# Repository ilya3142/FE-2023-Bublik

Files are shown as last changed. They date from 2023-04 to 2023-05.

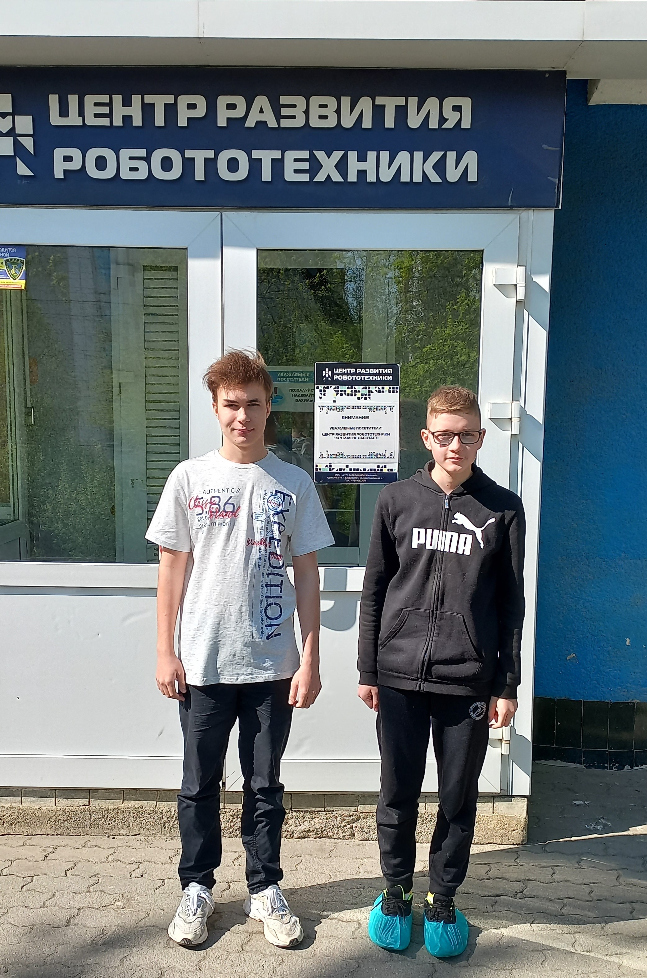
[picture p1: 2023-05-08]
Фото/Фото команды.jpg

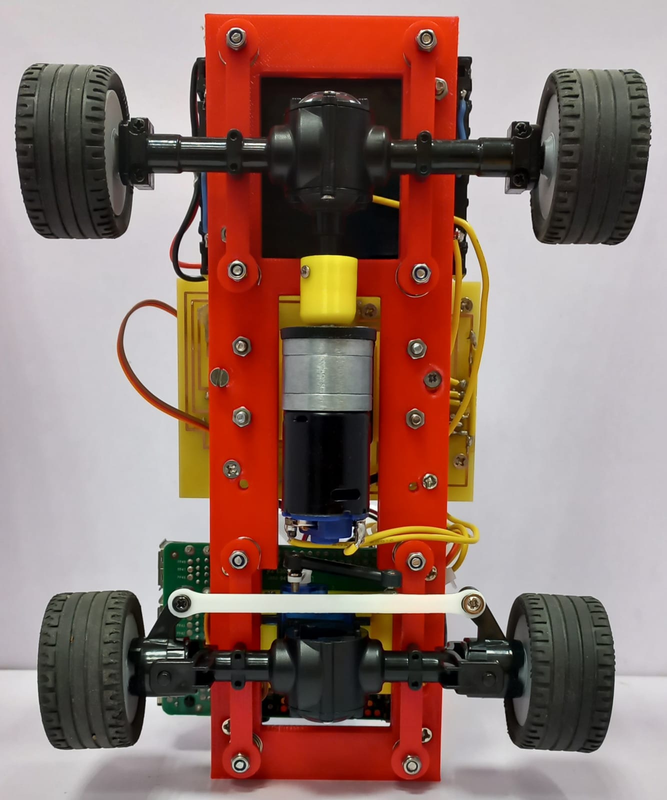
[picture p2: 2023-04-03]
Фото/вид снизу.jpg

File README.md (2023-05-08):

Расположение файлов, что находится в каждой папке

1. В папке 3D расположены модели деталей для нашего робота, которые мы сами моделировали и печатали на 3D принтере. Там есть следующие детали: диск (необходимо 4 шт. на одного робота), крепление под камеру (1 шт.), переходник с мотора (1 шт.) и рессора (4 шт.). 
2. В папке "src" расположены все фотографии, необходимые для пояснения того, как подключиться к нашему роботу и запустить программу. 
3. В папке "Видео" находится файл, загруженный на видеохостинг "YouTube", в котором показывается оба заезда (квалификационный и финальный) и краткое описание нашего робота. 
4. Папка "Код" содержит весь, необходимый для запуска, программный код, который включает в себя файлы: autostart.py (запуск программ квалификации и финала на соревнованиях), RobotAPI.py (считывание, вывод и редактирование изображения с камеры), Final.py (программа выступления в финальном заезде), kvalifikacia.py (программа выступления на квалификационном заезде), main.py (функции «нижнего кода») и start_robot.py (позволяет подключаться к роботу по сети Wi-Fi, загружать и запускать все программы). 
5. В папке "Технический журнал" находится вся документация, которая включает в себя:
	1. Реализация системы перемещения.
	2. Реализация системы питания и сенсоров.
	3. Реализация систем распознавания препятствий. 
 6. В папке "Фото" содержатся 6 фотографий робота с различных сторон и наша командная фотография.
 
Описание модулей кода

1. В программе «main.py» расположены функции «нижнего кода», а именно: 
	1. С Raspberry передает данные на драйвер мотора, светодиод.
	2. Передает показания с кнопки обратно на Raspberry.
2. Программа «start_robot.py» это приложение, позволяет подключаться к роботу по сети Wi-Fi, загружать и запускать все программы.
3. Файл «kvalificacia.py» содержит программу выступления на квалификационном заезде. 	Ниже представлено описания данного заезда: 
	Робот начинает движение по ПД регулятору считывая информацию о стенах с камеры. Когда он перестаёт видеть правую стену, он начинает поворачивать направо, а когда не видит левую, поворачивать налево. В процессе поворота робот должен увидеть на трассе первую одну из двух линий: либо синюю, либо оранжевую (с этого момента у робота включается счётчик линий того цвета, которую он увидел первым). Если он видит сначала синюю, то робот понимает, что движется против часовой стрелки, а если оранжевую, то по часовой. Во время движения вдоль каждой из 4 сторон, робот записывает время, за которое он проехал каждую прямую. Когда счётчик покажет, что робот увидел 12 раз синюю или оранжевую линию (в зависимости от направления движения), робот понимает, что проехал три круга, и ему нужно постепенно завершать заезд, он еще проезжает некоторое количество времени чтобы остановится идеально в зоне финиша, вычислив время проезда половины одной из двенадцати частей пути по записанному времени.
4. Файл «Final.py» содержит программу выступления в финальном заезде.
	Ниже представлено описание данного заезда:
	Робот начинает движение по ПД регулятору считывая информацию о стенах с камеры. Когда он перестаёт видеть правую стену, он начинает поворачивать направо, а когда не видит левую, поворачивать налево. В процессе поворота робот должен увидеть на трассе первую одну из двух линий: либо синюю, либо оранжевую (с этого момента у робота включается счётчик линий того цвета, которую он увидел первым). Если он видит сначала синюю, то робот понимает, что движется против часовой стрелки, а если оранжевую, то по часовой. Во время движения вдоль стен робот видит зелёные и красные знаки, если он видит зелёный знак, то объезжает его по левой стороне, а если красный – по правой. Когда счётчик покажет, что робот увидел 12 раз синюю или оранжевую линию (в зависимости от направления движения), робот понимает, что проехал три круга, и ему нужно постепенно завершать заезд, он еще проезжает некоторое количество времени чтобы остановится идеально в зоне финиша, вычислив время проезда половины одной из двенадцати частей пути по записанному времени.
5. Программа «autostart.py» необходима для запуска программ квалификации и финала на соревнованиях, сначала происходит автоматический запуск два раза квалификационного заезда, а затем два раза финального.
6. Файл «robotAPI.py» содержит функции, которые позволяют считывать и выводить картинку с камеры, делать определённые датчики на ней, которые необходимы для успешного проезда робота. 

Пошаговое объяснение, как подключиться к нашему роботу и запустить программу

1. Из папки "Код" на github скачиваем все файлы на компьютер. 
2. Загружаем файл "main.py" на Pyboard, для этого: подключаем Pyboard к компьютеру при помощи кабеля, находим на компьютере папку Pyboard и копируем туда файл "main.py". 
3. Открываем файл "start_robot.py" в PyCharm.
4. Далее запускаем этот файл.
5. Затем подключаемся к Raspberry нашего робота через сеть Wi-Fi. (https://github.com/ilya3142/FE-2023-Bublik/blob/main/src/image%201.png)
6. Затем у нас открывается окно "RoboStarter", где мы нажимаем кнопку "Connect to robot" и выбираем там нашего робота по названию.(https://github.com/ilya3142/FE-2023-Bublik/blob/main/src/image%202.png)
7. Далее мы нажимаем кнопку «Load Start», где мы можем выбрать и запустить программу, которая нам необходима: проезд финала, квалификации, или файл «autostart.py», в котором содержится одна из вышеперечисленных программ.

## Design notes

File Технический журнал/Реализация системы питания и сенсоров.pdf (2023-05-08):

### Реализация системы питания и сенсоров

### 1. Питание

| Напряжение | Ёмкость
Аккумулятор 18650 | 3.7 B | 3500 mAh
Аккумулятор 14500 | 3.7 В | 600 mAh
Батарейки AA | 1.2 В | 2100 mAh

Для питания нам было представлено три типа: аккумулятор 18650, аккумулятор 14500 и батарейки типа AA. Из них мы остановились на варианте аккумулятора 18650, так как у него наибольшая ёмкость и токоотдача, благодаря чему он дольше поддерживает работу. Выбрав аккумулятор, мы взяли три штуки и поместили их в отсек для того, чтобы получилось общее напряжение около 12 Вольт.

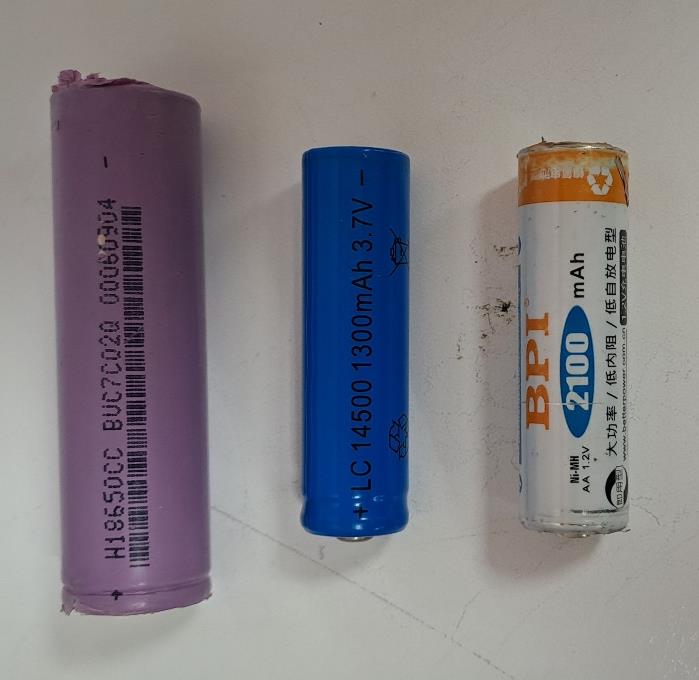
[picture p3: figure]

Слева направо:
1. Аккумулятор 18650
2. Аккумулятор 14500
3. Батарейка типа АА

### 2. Камера и Raspberry

Для того, чтобы распозновать все объекты на соревновании нам необходима камера. У нас было представлено три камеры на выбор:

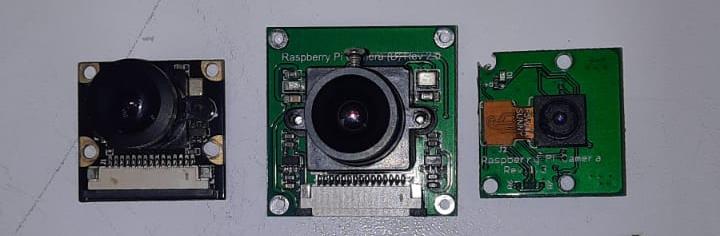
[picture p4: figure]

Слева направо:

1. RPi Camera G
2. RPi Camera B
3. RPi Camera Board

Исходя из их характеристик, мы пришли к решению выбрать камеру под номером 1, потому что она обладает наибольшим углом обзора, то есть является широкоугольной, что позволяет нам хорошо видеть бортики на игровом поле.

Для обработки и считывания изображения с камеры мы используем одноплатный компьютер Raspberry Pi 3B. Для распознавания объектов на соревновательном поле, мы используем язык программирования Python и библиотеку OpenCV. Благодаря им, мы можем на камере выделить области под датчики и распознавать объекты в разных частях изображения.

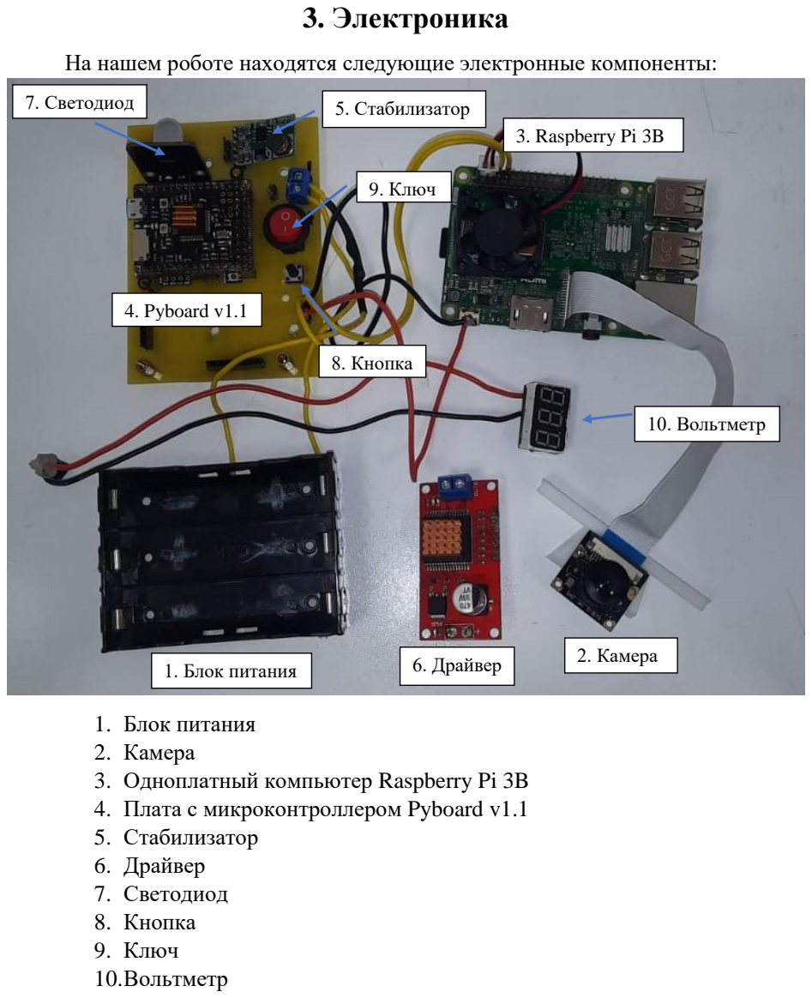
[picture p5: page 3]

### 3. Электроника

На нашем роботе находятся следующие электронные компоненты:

1. Блок питания
2. Камера
3. Одноплатный компьютер Raspberry Pi 3B
4. Плата с микроконтроллером Pyboard v1.1
5. Стабилизатор
6. Драйвер
7. Светодиод
8. Кнопка
9. Ключ
10.Вольтметр
10. Вольтметр
1. Блок питания | 6. Драйвер | 2. Камера
3. Raspberry Pi 3B
4. Pyboard v1.1
5. Стабилизатор 7. Светодиод
8. Кнопка
9. Ключ

### 4. Электрическая схема

Ниже представлена электрическая схема, сделанная на платформе EasyEDA, по ней вы можете разобраться, какие компоненты куда необходимо подключать:

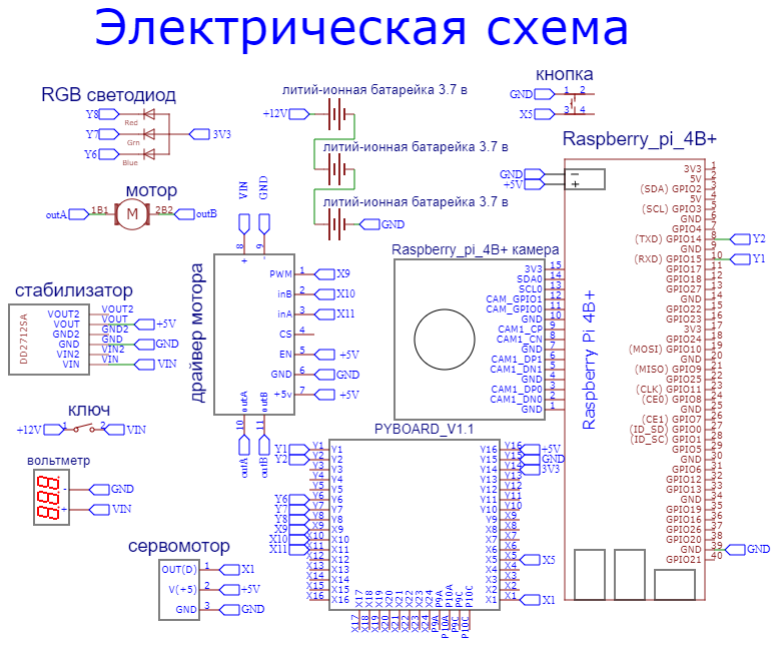
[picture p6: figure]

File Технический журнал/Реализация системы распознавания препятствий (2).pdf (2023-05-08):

Реализация системы распознавания препятствий

### 1. Квалификационный заезд

Ниже представлено описание проезда робота на квалификационном заезде:

Робот начинает движение по ПД регулятору считывая информацию о стенах с камеры. Когда он перестаёт видеть правую стену, он начинает поворачивать направо, а когда не видит левую, поворачивать налево. В процессе поворота робот должен увидеть на трассе первую одну из двух линий: либо синюю, либо оранжевую (с этого момента у робота включается счётчик линий того цвета, которую он увидел первым). Если он видит сначала синюю, то робот понимает, что движется против часовой стрелки, а если оранжевую, то по часовой. Во время движения вдоль каждой из 4 сторон, робот записывает время, за которое он проехал каждую прямую. Когда счётчик покажет, что робот увидел 12 раз синюю или оранжевую линию (в зависимости от направления движения), робот понимает, что проехал три круга, и ему нужно постепенно завершать заезд, он еще проезжает некоторое количество времени чтобы остановится идеально в зоне финиша, вычислив время проезда половины одной из двенадцати частей пути по записанному времени.

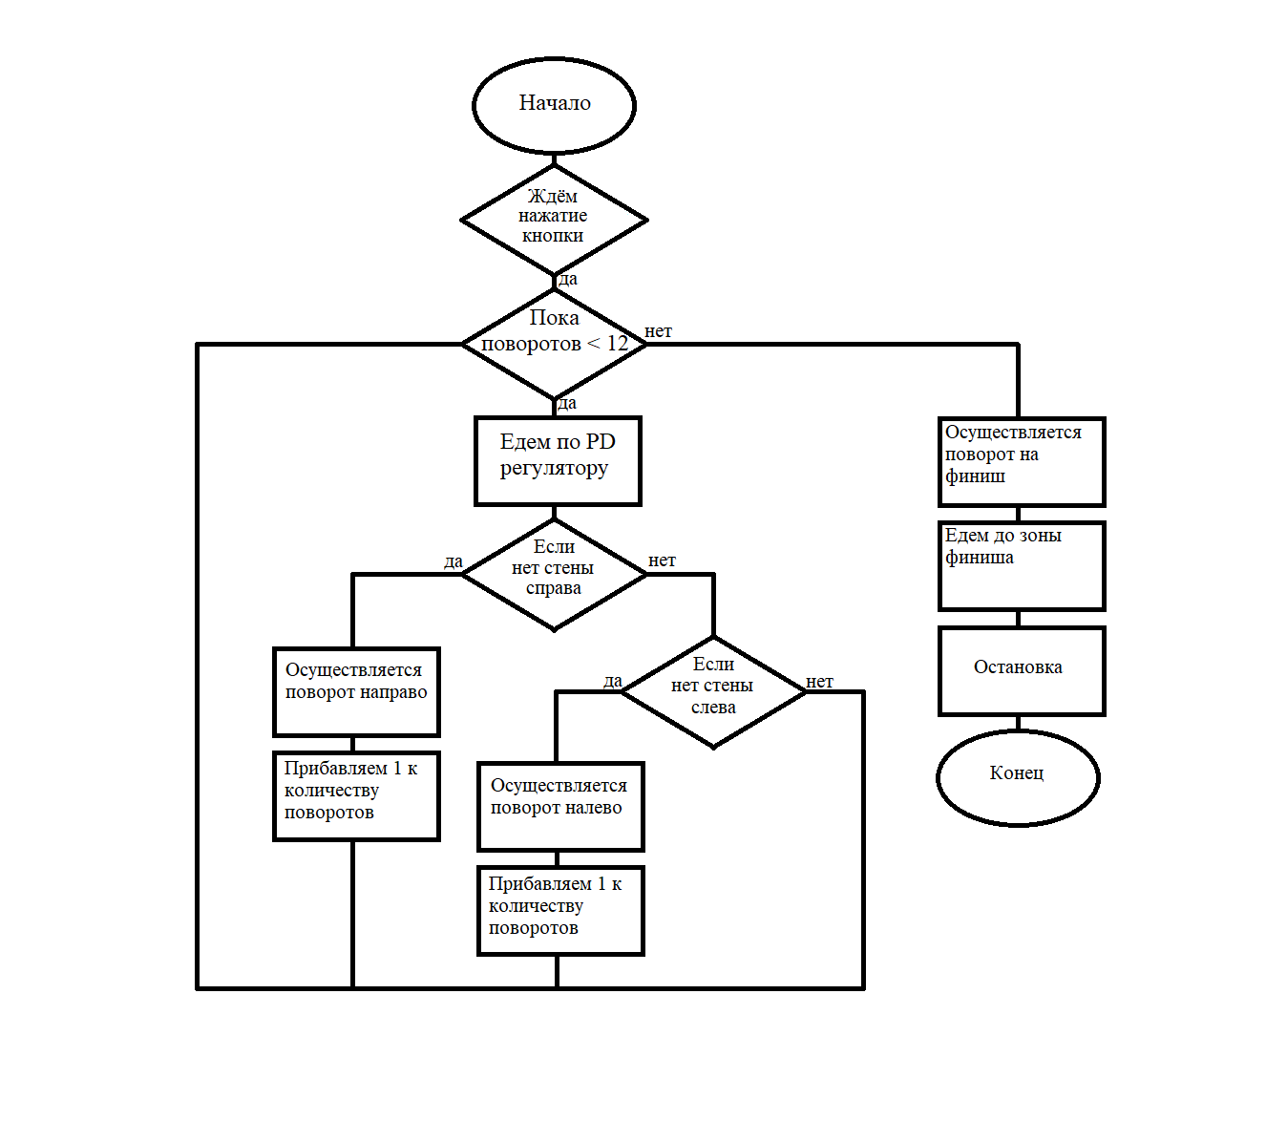
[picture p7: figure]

### 2. Финальный заезд

Ниже представлено описание проезда робота на финальном заезде:

Робот начинает движение по ПД регулятору считывая информацию о стенах с камеры. Когда он перестаёт видеть правую стену, он начинает поворачивать направо, а когда не видит левую, поворачивать налево. В процессе поворота робот должен увидеть на трассе первую одну из двух линий: либо синюю, либо оранжевую (с этого момента у робота включается счётчик линий того цвета, которую он увидел первым). Если он видит сначала синюю, то робот понимает, что движется против часовой стрелки, а если оранжевую, то по часовой. Во время движения по трассе робот видит зелёные и красные знаки, если он видит зелёный знак, то объезжает его по левой стороне, а если красный – по правой. Когда счётчик покажет, что робот увидел 12 раз синюю или оранжевую линию (в зависимости от направления движения), робот понимает, что проехал три круга, и ему нужно постепенно завершать заезд, он еще проезжает некоторое количество времени чтобы остановится идеально в зоне финиша, вычислив время проезда половины одной из двенадцати частей пути по записанному времени.

### 3. Распознавание знаков

На камере робот ищет красные и зелёные знаки в области интереса, которая находится в центре. При нахождении любого знака робот обводит больший знак соответствующим цветом (красный знак – жёлтая рамка, зелёный знак – розовая рамка).

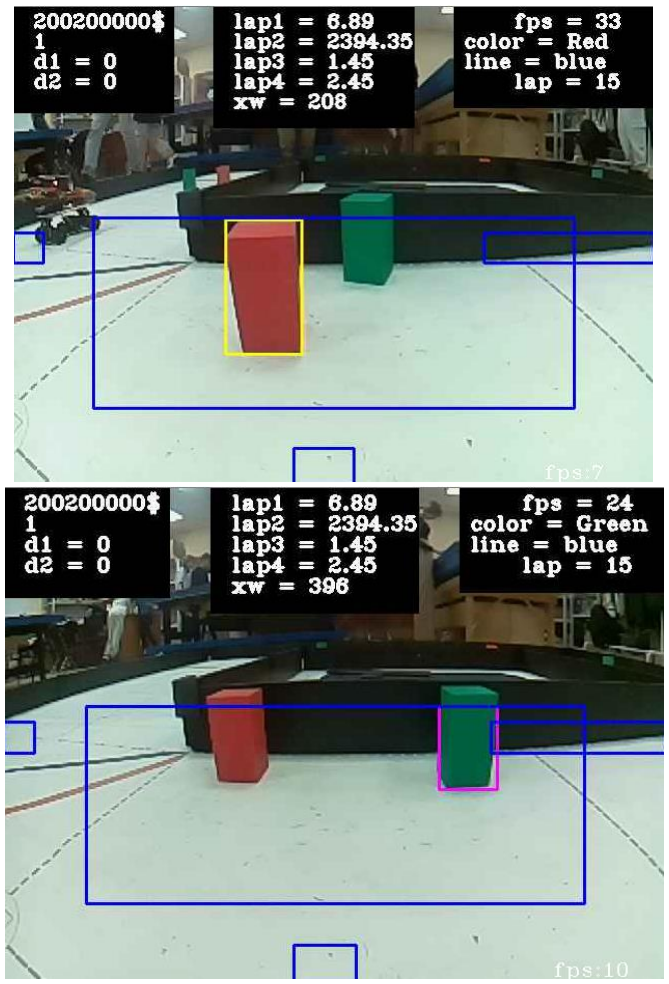
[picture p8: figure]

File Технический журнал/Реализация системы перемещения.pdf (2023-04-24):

### Реализация системы перемещения

### 1. Выбор моторов для движения

Изначально у нас было представлено на выбор 3 мотора:

1. GM25-370 на 6 вольт и 210 оборотов в минуту.

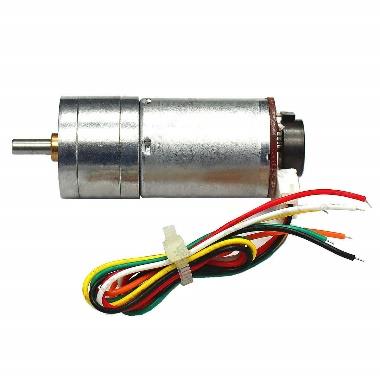
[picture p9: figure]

2. CH-N20-3 – 6 вольт и 500 оборотов в минуту.

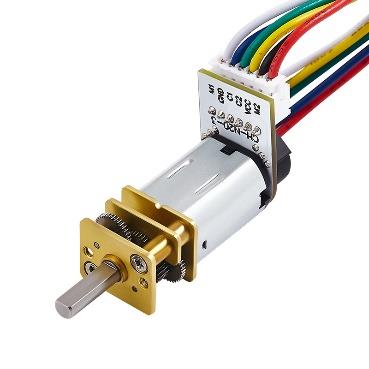
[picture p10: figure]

3. CHR-GM25-370 на 12 вольт и 980 оборотов в минуту.

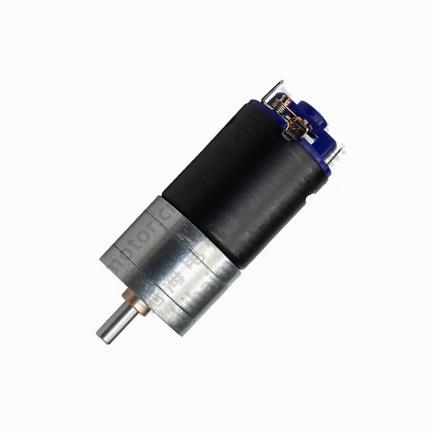
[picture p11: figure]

Мы выбрали третий вариант - CHR-GM25-370, потому что он обладает самыми хорошими и выгодными для нас характеристиками, а именно: металлической цилиндрической шестернёй, сильный магнитный крутящий момент и достаточно большой скоростью (980 об/мин). Также у него есть отдельное крепление, под которое удобно проектировать кузов.

### 2. Выбор моторов для руления

Нам также было представлено на выбор 3 мотора для руления:

1. Tower Pro SG90: Сервопривод с диапазоном 0-180° обладает компактными размерами, напряжение 3,5-6 вольт, весом 9 грамм и обладает большим крутящим моментом (до 1,6 кг·см). Механизм сервопривода выполнен из пластика.

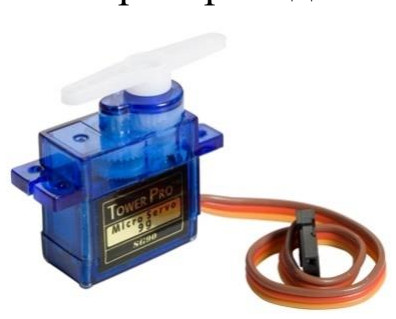
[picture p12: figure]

2. TIANKONGRC MG90D: управляется по сигналу PDM, способен удерживать угол от 0 до 180° и обладает крутящим моментом до 2,1 кг·см.

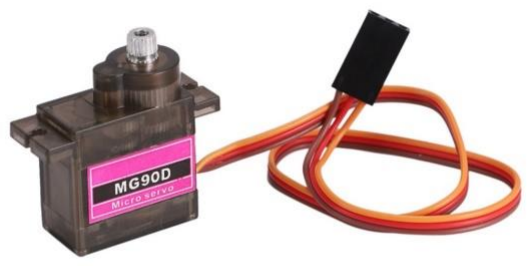
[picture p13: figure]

3. EMAX ES08A: рабочее напряжение 4,8-6 вольт, крутящий момент до 1,8 кг·см, Длина сервопривода от выхода корпуса до вилки: 230 мм, механизм выполнен из пластика

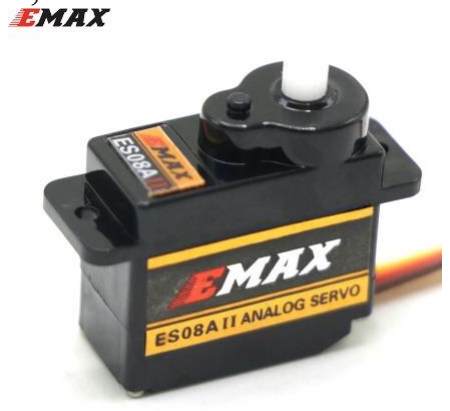
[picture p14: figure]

Все представленные модели обладают схожими характеристиками, поэтому мы выбрали первый вариант - Tower Pro SG90 из-за того, что это самый распространённый мотор, который, при необходимости, всегда можно заменить.

### 3. Подвеска

Мы выбирали между двумя видами подвески:

1. Мостовая: это такая подвеска, в которой ось связывает между собой два колеса. Колеса связаны через дифференциал.

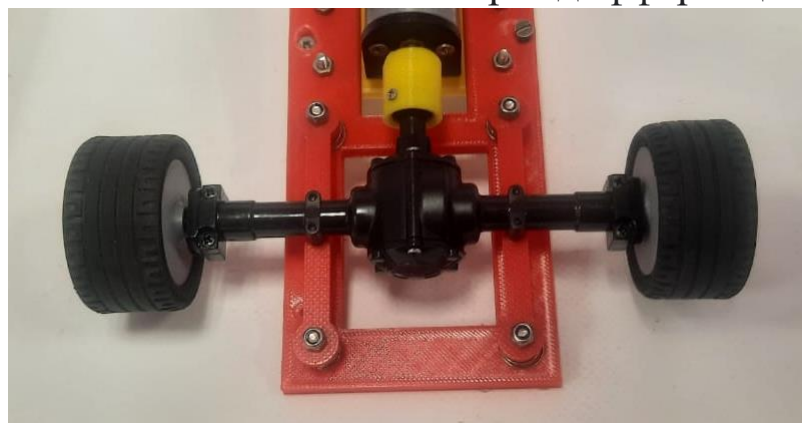
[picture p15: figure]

2. Независимая: это такая подвеска, в которой колеса одной оси не связаны друг с другом, и изменение положения одного колеса не оказывает влияния на другое.

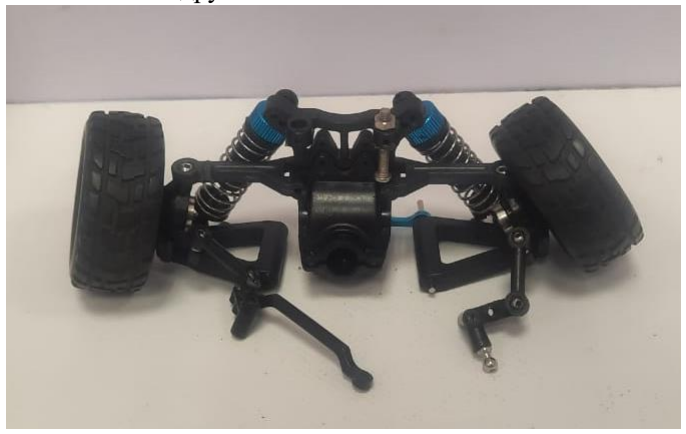
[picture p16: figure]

Для мостовой подвески было гораздо проще создать кузов, она была удобнее в креплении к основной раме робота, поэтому мы её и выбрали.

### 4. Колёса

При переходе к этому этапу мы столкнулись с проблемой, что колёса, которые шли в комплекте с подвеской оказались слишком большие для нашей машинки (56x25):

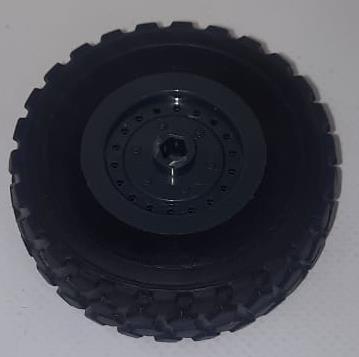
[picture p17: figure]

И поэтому мы спроектировали и распечатали на 3D принтере новые диски (31x20) оптимального размера и вставили их в шины (42x21):

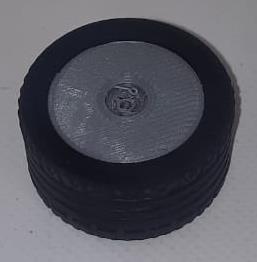
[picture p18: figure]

### 5. Рама робота

Для соединения всех механизмов и деталей, таких как рессоры, муфта и подвеска, в одно целое, мы спроектировали и распечатали на 3D принтере раму, которая связывает все элементы робота.

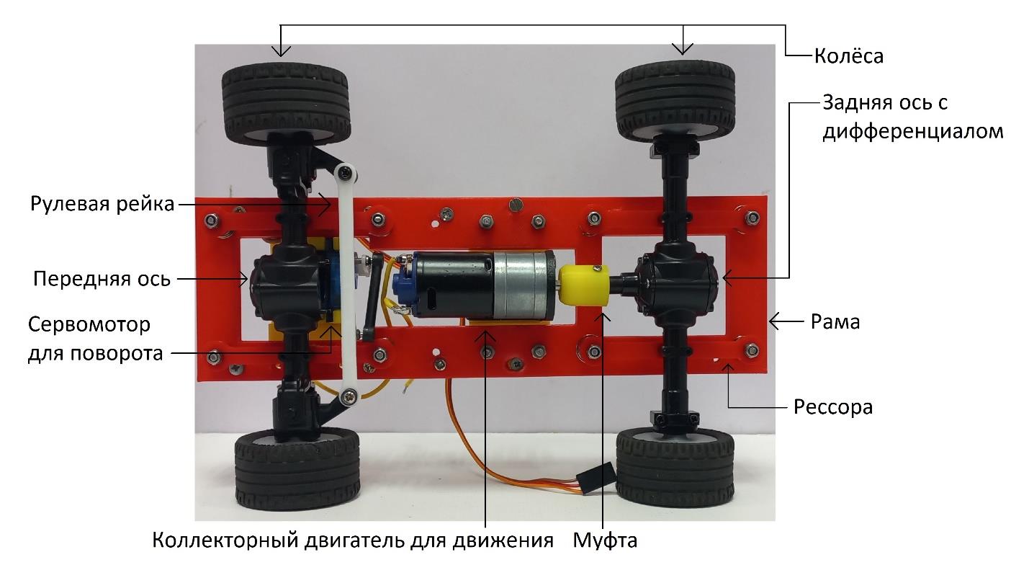
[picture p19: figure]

### 6. Механическая схема автомобиля

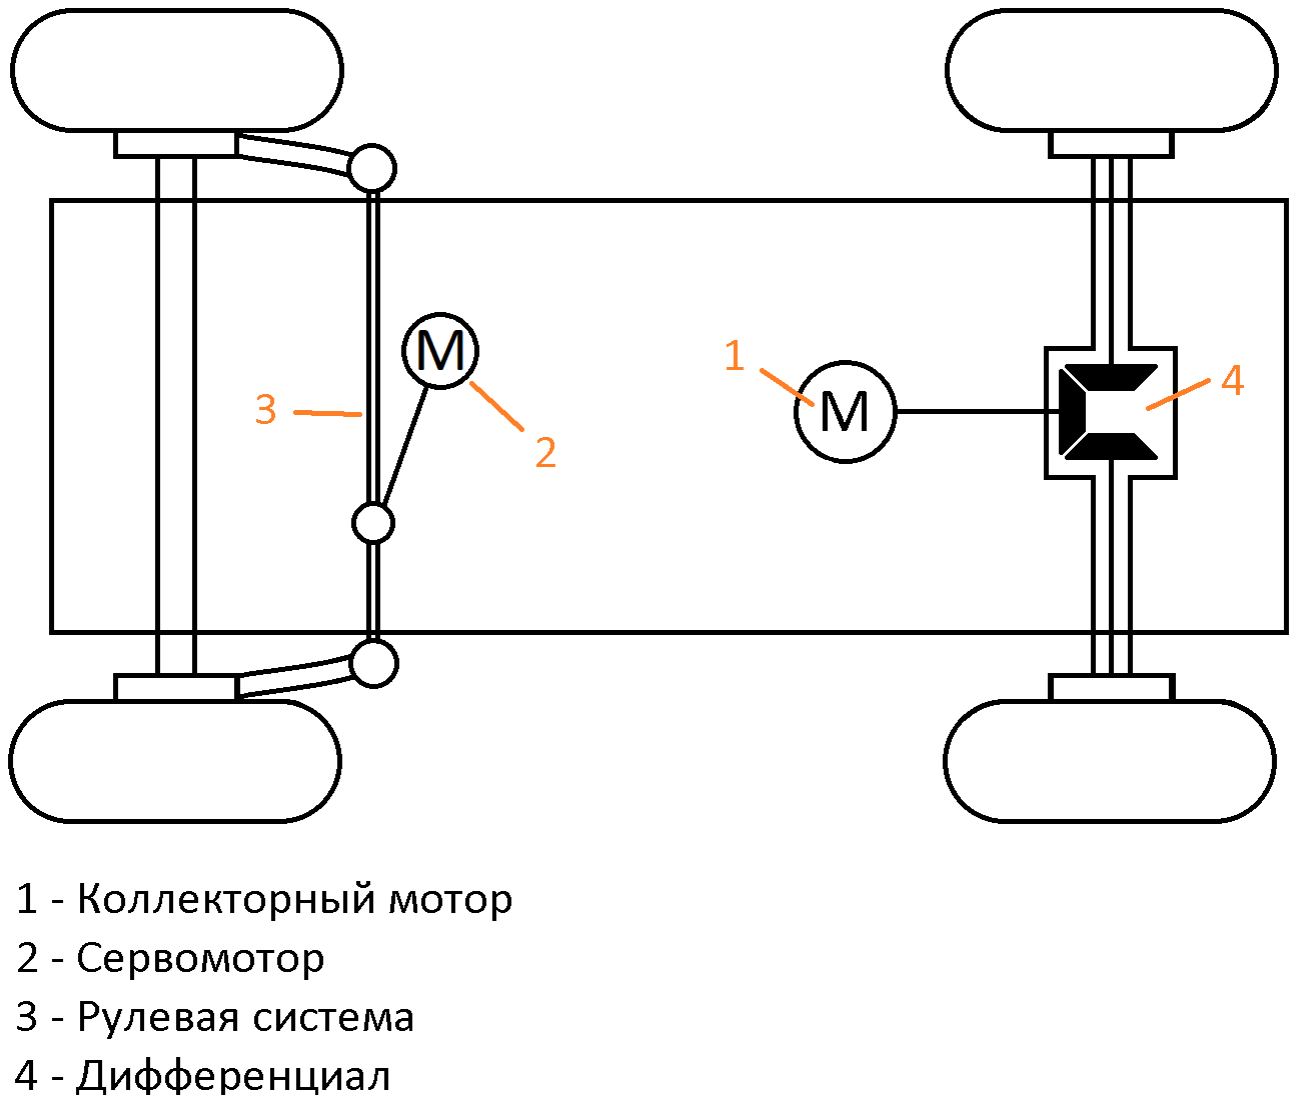
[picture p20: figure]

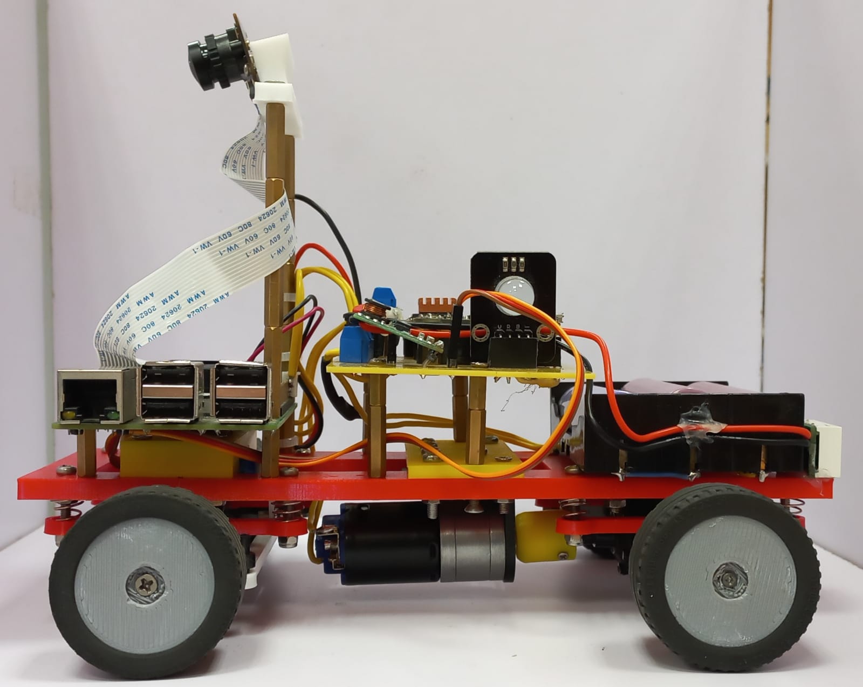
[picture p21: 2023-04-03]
Фото/вид слева.jpg

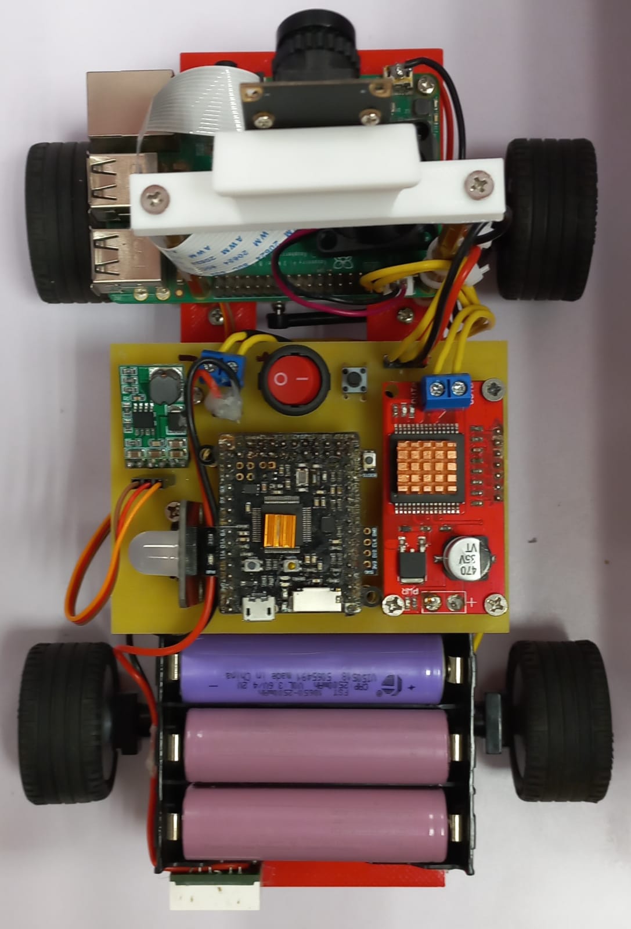
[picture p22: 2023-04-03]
Фото/вид сверху.jpg

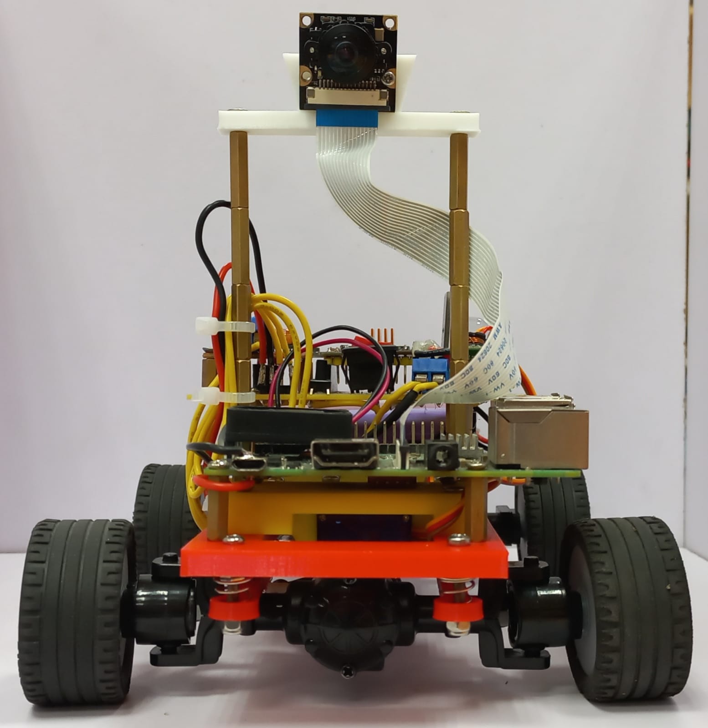
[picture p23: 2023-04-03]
Фото/вид спереди.jpg

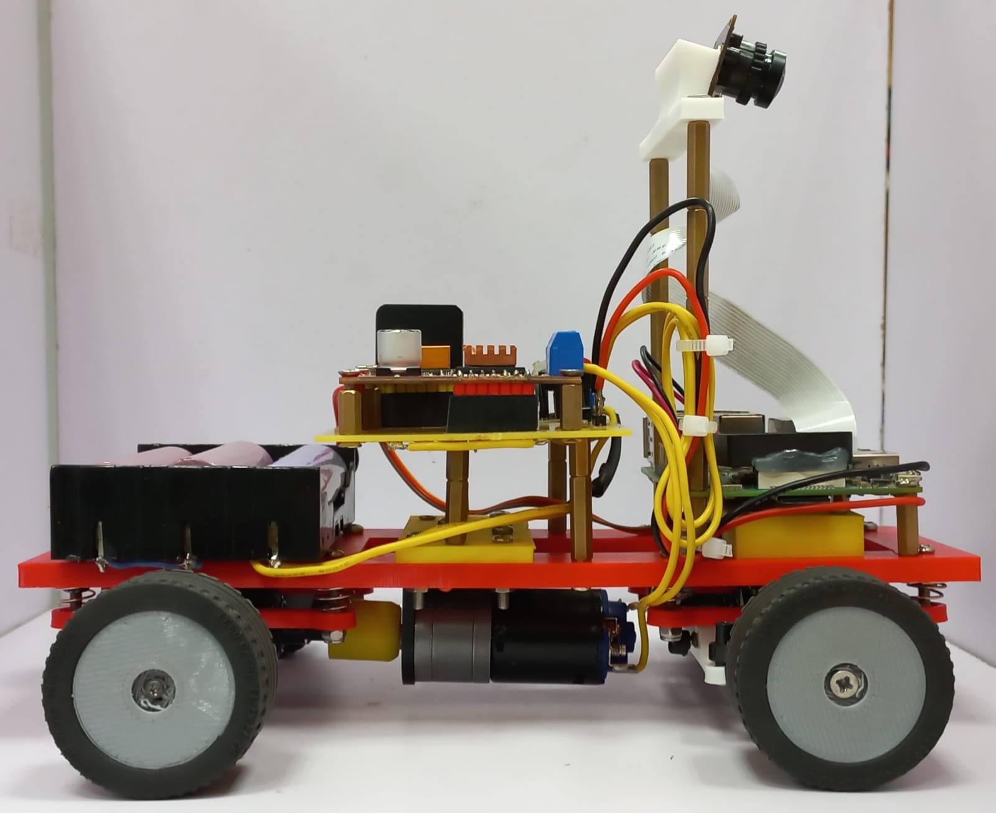
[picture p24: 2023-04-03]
Фото/вид справа.jpg

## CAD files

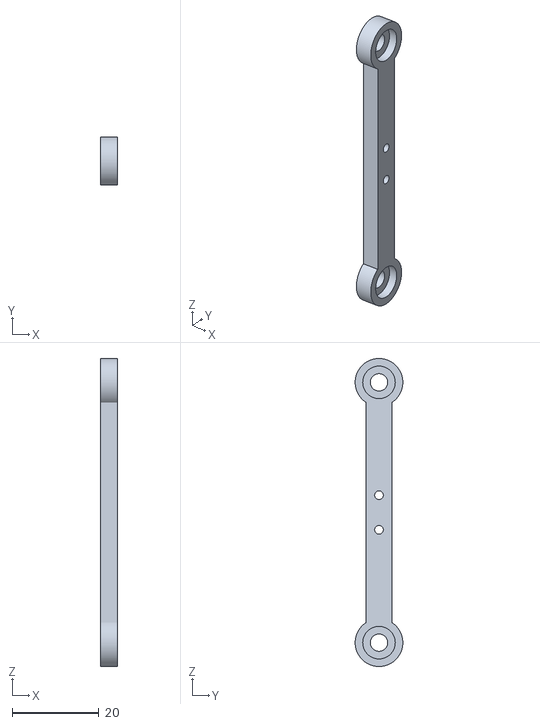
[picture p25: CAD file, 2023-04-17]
3D/рессора.stl
4.00 x 11.0 x 71.0

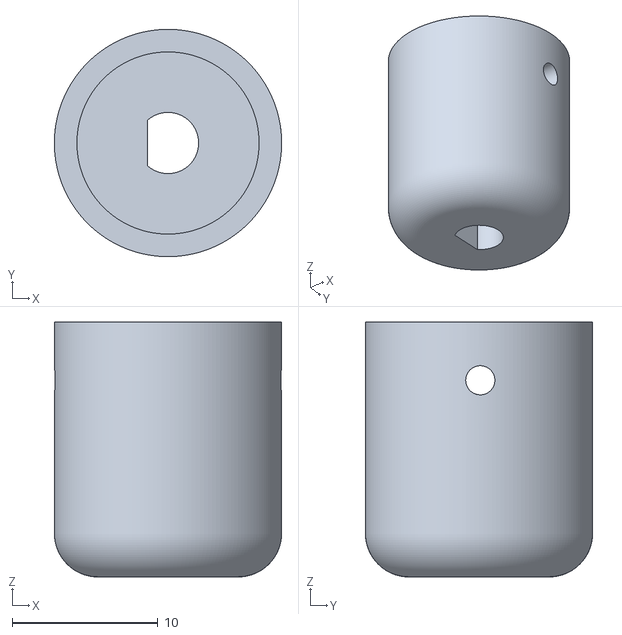
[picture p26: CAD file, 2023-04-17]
3D/переходник с мотора.stl
15.6 x 15.6 x 17.5

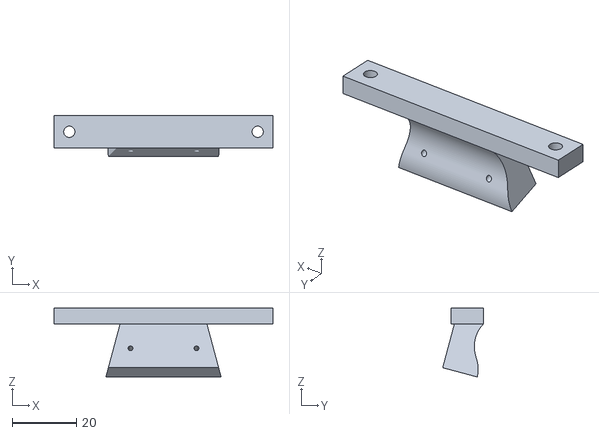
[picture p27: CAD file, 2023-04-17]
3D/крепление под камеру.stl
68.0 x 12.6 x 21.4

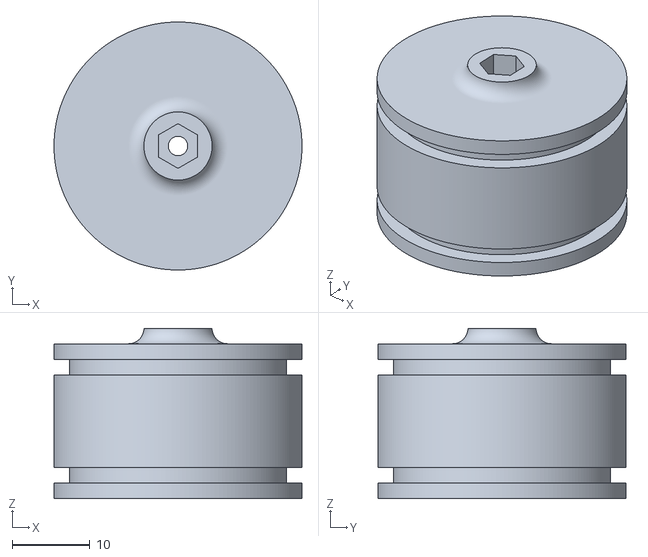
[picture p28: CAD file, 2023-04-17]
3D/диск.stl
32.0 x 32.0 x 22.0

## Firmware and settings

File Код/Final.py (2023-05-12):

import cv2
import RobotAPI as rapi
import numpy as np
import serial
import time
from array import *

tim_s = time.time()
tim_l = time.time()
tp = time.time()
ts = time.time()
tz = time.time()
tr = time.time()
tg = time.time()

fst = False

low_black=np.array([0,0,0]) # HSV чёрного
up_black=np.array([70,255,27])

low_red=np.array([0,130,0]) # HSV красного
up_red=np.array([5,220,255])

low_blue=np.array([93,108,56]) # HSV синего
up_blue=np.array([128,255,139])

low_orange=np.array([0,110,100]) # HSV оранжеаого
up_orange=np.array([20,255,182])

low_green=np.array([74, 168, 67]) # HSV зелёного
up_green=np.array([99, 255, 145])

port = serial.Serial("/dev/ttyS0", baudrate=115200, stopbits=serial.STOPBITS_ONE)
robot = rapi.RobotAPI(flag_serial=False)
robot.set_camera(100, 640, 480)

direction = "None" # направление движения

vrm= [0, 0, 0, 0]
vi = 0
message = ""
fps = 0
fps1 = 0
fps_time = 0

art = 0

x_zn = 0
y_zn = 0
w_zn = 0
h_zn = 0

r_zn = 0
g_zn = 0

zn_old = 0
zn_t = 0
wzn_old = 0


e_old = 0
e_old_zn = 0

kp = 0.15
kd = 0.15

d1 = 0
d2 = 0
d1old = 0
d2old = 0
d1t = 0
d2t = 0

color = 'Green'
line1 = 'Orange'
lap = 0

speed = 0 # скорость
serv = 0 # угол поворота сервомотора
rgb = "111" # сообщение для светодиода
inn = ""


xleft = 160
xright = 470

def znak(frame): # распознавание знаков
    global x_zn, y_zn, h_zn, w_zn,color, tz, xleft, xright, zn_t, zn_old, wzn_old
    x_zn, y_zn, h_zn, w_zn = 0, 0, 0, 0
    x1 = 80 # область интереса
    x2 = 560
    y1 = 210
    y2 = 400
    dat = frame[y1:y2, x1:x2]
    hsv = cv2.cvtColor(dat, cv2.COLOR_BGR2HSV) # преобразование BGR в HSV


    mask = cv2.inRange(hsv, low_red, up_red) # создание маски
    imd, contours, hod = cv2.findContours(mask, cv2.RETR_TREE, cv2.CHAIN_APPROX_NONE) # находим на маске контуры
    xx, yy, ww, hh = 0,0,0,0
    for contor in contours:
        x, y, w, h = cv2.boundingRect(contor) # обводим контуры
        if h*w > 100 and h*w > hh*ww:
            xx, yy, ww, hh = x,y,w,h




    mask1 = cv2.inRange(hsv, low_green, up_green) # создание маски
    imd, contours, hod = cv2.findContours(mask1, cv2.RETR_TREE, cv2.CHAIN_APPROX_NONE) # находим контуры на маске
    xq, yq, wq, hq = 0, 0, 0, 0
    for contor in contours:
        x, y, w, h = cv2.boundingRect(contor) # обводим контуры
        if h*w > 100 and h*w > hq*wq:
            xq, yq, wq, hq = x,y,w,h


    color = 'None'

    if hh > 0 or hq > 0: # изменение областей интересов для распознавания стен

        if yy + hh > yq + hq: # объезд знаков
            cv2.rectangle(dat, (xx, yy), (xx + ww, yy + hh), (0, 255, 255), 2) # обводим найденные когтуры
            x_zn, y_zn, w_zn, h_zn = xx, yy, ww, hh
            color = 'Red'
            if direction == "blue": # направление движения
                xleft = 30

        else:
            cv2.rectangle(dat, (xq, yq), (xq + wq, yq + hq), (255, 0, 255), 2) # обводим найденные контуры
            x_zn, y_zn, w_zn, h_zn = xq, yq, wq, hq
            color = 'Green'
            if direction == "orange": # направление движения
                xright = 610

        tz = time.time()
        zn_old = x_zn
        wzn_old = w_zn

    else:
        if zn_t + 0.5 > time.time():
            x_zn = zn_old
            w_zn = wzn_old

        if tz + 0.5 < time.time():
            xleft = 160
            xright = 470


def line(frame): # распознаваие стен (подробнее в kvalifikacia)
    global d1, d2, d1old, d2old, d1t, d2t, xleft, xright
    x3 = 0
    x4 = xleft
    y3 = 225
    y4 = 255
    dat = frame[y3:y4, x3:x4]
    hsv = cv2.cvtColor(dat, cv2.COLOR_BGR2HSV)
    mask = cv2.blur(cv2.inRange(hsv, low_black, up_black), (3, 3))
    imd, contours, hod = cv2.findContours(mask, cv2.RETR_TREE, cv2.CHAIN_APPROX_NONE)
    xe, ye, we, he = 0, 0, 0, 0
    d1 = 0
    for contor in contours:
        x, y, w, h = cv2.boundingRect(contor)
        a = cv2.contourArea(contor)
        if a > 200 and x + w > xe + we:
            xe, ye, we, he = x, y, w, h
    d1 = xe + we
    cv2.rectangle(dat, (xe, ye), (xe + we, ye + he), (255, 255, 0), 2)
    cv2.rectangle(frame, (x3, y3), (x4, y4), (255, 0, 0), 2)
    if d1 == 0:
        if time.time() - d1t <= 0.05:
            d1 = d1old
    else:
        d1old = d1
        d1t = time.time()

    x5 = xright
    x6 = 640
    y5 = 225
    y6 = 255

    dat = frame[y5:y6, x5:x6]
    hsv = cv2.cvtColor(dat, cv2.COLOR_BGR2HSV)
    mask = cv2.blur(cv2.inRange(hsv, low_black, up_black), (3, 3))
    imd, contours, hod = cv2.findContours(mask, cv2.RETR_TREE, cv2.CHAIN_APPROX_NONE)
    xr, yr, wr, hr = 150, 0, 0, 0
    d2 = 0
    for contor in contours:
        x, y, w, h = cv2.boundingRect(contor)
        a = cv2.contourArea(contor)
        if a > 200 and 150 - x> 150 - xr:
            xr, yr, wr, hr = x, y, w, h
    d2 = 150 - xr
    cv2.rectangle(dat, (xr, yr), (xr + wr, yr + hr), (255, 255, 0), 2)

    cv2.rectangle(frame, (x5, y5), (x6, y6), (255, 0, 0), 2)
    if d2 == 0:
        if time.time() - d2t <= 0.05:
            d2 = d2old
    else:
        d2old = d2
        d2t = time.time()

def povorot(frame): # распознавание оранжевых и синих линий на трассе (подробнее в kvalifikacia)
    global d1,d2,lap,tp, direction, vi, vrm, art, rgb
    x7 = 280
    x8 = 340
    y7 = 440
    y8 = 480
    dat = frame[y7:y8, x7:x8]
    hsv = cv2.cvtColor(dat, cv2.COLOR_BGR2HSV)

    if direction == "None":
        mask = cv2.inRange(hsv, low_orange, up_orange)
        imd, contours, hod = cv2.findContours(mask, cv2.RETR_TREE, cv2.CHAIN_APPROX_NONE)
        xx1, yy1, ww1, hh1 = 0, 0, 0, 0
        for contor in contours:
            x, y, w, h = cv2.boundingRect(contor)
            if h * w > 50 and h * w > hh1 * ww1:
                cv2.rectangle(dat, (x, y), (x + w, y + h), (0, 255, 0), 2)
                xx1, yy1, ww1, hh1 = x, y, w, h
        cv2.rectangle(dat, (xx1, yy1), (xx1 + ww1, yy1 + hh1), (0, 255, 255), 2)

        mask = cv2.inRange(hsv, low_blue, up_blue)
        imd, contours, hod = cv2.findContours(mask, cv2.RETR_TREE, cv2.CHAIN_APPROX_NONE)
        xx2, yy2, ww2, hh2 = 0, 0, 0, 0
        for contor in contours:
            x, y, w, h = cv2.boundingRect(contor)
            if h * w > 50 and h * w > hh2 * ww2:
                cv2.rectangle(dat, (x, y), (x + w, y + h), (0, 255, 0), 2)
                xx2, yy2, ww2, hh2 = x, y, w, h
        cv2.rectangle(dat, (xx2, yy2), (xx2 + ww2, yy2 + hh2), (0, 255, 255), 2)

        if hh1>0 or hh2 > 0: # счёт кругов пройденных роботом
            if tp + 0.5 < time.time():

                lap += 1
                if hh1 > 0: # распознавание направления движения
                    direction = "orange"
                    rgb = "110"
                if hh2 > 0:
                    direction = "blue"
                    rgb = "001"
                vrm[vi] = round(time.time() - tp, 2)
                vi += 1
                tp = time.time()
                art = time.time()


    elif direction == "orange":
        mask = cv2.inRange(hsv, low_orange, up_orange)
        imd, contours, hod = cv2.findContours(mask, cv2.RETR_TREE, cv2.CHAIN_APPROX_NONE)
        xx1, yy1, ww1, hh1 = 0, 0, 0, 0
        for contor in contours:
            x, y, w, h = cv2.boundingRect(contor)
            if h * w > 50 and h * w > hh1 * ww1:
                cv2.rectangle(dat, (x, y), (x + w, y + h), (0, 255, 0), 2)
                xx1, yy1, ww1, hh1 = x, y, w, h
        cv2.rectangle(dat, (xx1, yy1), (xx1 + ww1, yy1 + hh1), (0, 255, 255), 2)
        if hh1 > 0:
            if tp + 0.5 < time.time():
                rgb = "110"
                art = time.time()

                lap += 1
                vrm[vi] = round(time.time() - tp, 2)
                vi += 1
                if vi > 3:
                    vi = 0
                tp = time.time()

    else:
        mask = cv2.inRange(hsv, low_blue, up_blue)
        imd, contours, hod = cv2.findContours(mask, cv2.RETR_TREE, cv2.CHAIN_APPROX_NONE)
        xx2, yy2, ww2, hh2 = 0, 0, 0, 0
        for contor in contours:
            x, y, w, h = cv2.boundingRect(contor)
            if h * w > 50 and h * w > hh2 * ww2:
                cv2.rectangle(dat, (x, y), (x + w, y + h), (0, 255, 0), 2)
                xx2, yy2, ww2, hh2 = x, y, w, h
        cv2.rectangle(dat, (xx2, yy2), (xx2 + ww2, yy2 + hh2), (0, 255, 255), 2)

        if hh2 > 0:
            if tp + 0.5 < time.time():
                rgb = "001"
                art = time.time()
                lap += 1
                vrm[vi] = round(time.time() - tp, 2)
                vi += 1
                if vi > 3:
                    vi = 0
                tp = time.time()


    cv2.rectangle(frame, (x7, y7), (x8, y8), (255, 0, 0), 2)

def PD(): # ПД регулятор для движения по трассе
    global e_old, d1, d2
    kp = 0.15 # коэфиценты
    kd = 0.15
    e = d2 - d1
    Up = e * kp
    Ud = (e - e_old) * kd
    e_old = e
    U = Up + Ud
    return U

def PD_zn(): # ПД регулятор для движения по трассе с определением знаков
    global e_old_zn, x_zn, y_zn, w_zn, h_zn, color, tg, tr
    kp = 0.15 # коэфиценты
    kd = 0.15
    prib = (y_zn+h_zn)*1.1
    if color == "Red":
        e = (220 - prib) - (x_zn + w_zn)
    if color == "Green":
        e = (260 + prib) - x_zn
    Up = e * kp
    Ud = (e - e_old_zn) * kd
    e_old_zn = e
    U = Up + Ud
    return U


while 1: # цикл
    key = robot.get_key()
    frame = robot.get_frame(wait_new_frame=1)
    # запуск функций
    znak(frame)
    line(frame)
    povorot(frame)
    if art + 0.5 <= time.time() and fst:
        rgb = "000"

    serv = 0
    if speed > 0:
        if h_zn > 0:
            serv = PD_zn()
        else:
            serv = PD()
            if direction == "blue" and d1 == 0:
                serv = 40
            if direction == "orange" and d2 == 0:
                serv = -40
            if d1 == 0 and d2 == 0 and direction == "blue":
                serv = 40
            if d1 == 0 and d2 == 0 and direction == "orange":
                serv = -40

    if lap == 12: # остановка на финише
        if ts + vrm[0]*0.6 < time.time():
            speed = 0
    else:
        ts=time.time()
    # отправка сообщений RaspBerry
    message = str(int(speed) + 200) + str(int(serv) + 200) + rgb+'$'
    port.write(message.encode("utf-8"))


    if port.in_waiting > 0:
        inn = ""
        t = time.time()
        while 1:
            a = str(port.read(), "utf-8")
            if a != "$":
                inn += a
            else:
                break
            if t + 0.02 < time.time():
                break
        port.reset_input_buffer()

    if inn == "0" and tim_s + 1 < time.time():
        tim_s = time.time()
        if speed == 0:
            fst = True
            speed = 80
        else:
            speed = 0

    if lap >= 12: # остановка на финише
        if tim_l + 5 < time.time():
            speed = 0
    else:
        tim_l = time.time()

    fps1 += 1 # счётчик fps
    if time.time() > fps_time + 1:
        fps_time = time.time()
        fps = fps1
        fps1 = 0
    x1 = 80
    x2 = 560
    y1 = 210
    y2 = 400
    cv2.rectangle(frame, (x1, y1), (x2, y2), (255, 0, 0), 2) # рисуем прямоугольники на камере
    cv2.rectangle(frame, (0, 0), (0 + 160, 0 + 105), (0, 0, 0), -1)
    cv2.rectangle(frame, (440, 0), (440 + 200, 0 + 100), (0, 0, 0), -1)
    robot.text_to_frame(frame, message, 20, 20) # выыодим на камеру информацию
    robot.text_to_frame(frame, inn, 20, 40)
    robot.text_to_frame(frame, 'fps = ' + str(fps), 500, 20)
    robot.text_to_frame(frame, 'd1 = ' + str(d1), 20, 60)
    robot.text_to_frame(frame, 'd2 = ' + str(d2), 20, 80)
    robot.text_to_frame(frame, 'color = ' + str(color), 450, 40)
    robot.text_to_frame(frame, 'line = ' + str(direction), 450, 60)
    robot.text_to_frame(frame, 'lap = ' + str(lap), 500, 80)

    cv2.rectangle(frame, (200, 0), (400, 120), (0, 0, 0), -1)
    robot.text_to_frame(frame, 'lap1 = ' + str(vrm[0]), 220, 20)
    robot.text_to_frame(frame, 'lap2 = ' + str(vrm[1]), 220, 40)
    robot.text_to_frame(frame, 'lap3 = ' + str(vrm[2]), 220, 60)
    robot.text_to_frame(frame, 'lap4 = ' + str(vrm[3]), 220, 80)
    robot.text_to_frame(frame, 'xw = ' + str(x_zn+w_zn), 220, 100)

    robot.set_frame(frame, 40)

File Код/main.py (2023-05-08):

from pyb import delay, Pin, ADC, Timer, UART, LED
from machine import UART
uart = UART(6, 115200, stop=1)
inn = ""
speed = 0
serv = 0
r = 0
g = 0
b = 0
sv_r = Pin('Y8', Pin.OUT_PP)
sv_b = Pin('Y6', Pin.OUT_PP)
sv_g = Pin('Y7', Pin.OUT_PP)
sv_r.high()
sv_b.high()
sv_g.high()

kn = Pin('X5', Pin.IN, Pin.PULL_UP)

servo1 = pyb.Servo(1)
servo1.angle(serv)

p = Pin('X9')
prv = Pin('X10', Pin.OUT_PP)
lev = Pin('X11', Pin.OUT_PP)
prv.low()
lev.high()



tim = Timer(4, freq=1000)
motor = tim.channel(1, Timer.PWM, pin=p)
motor.pulse_width_percent(speed)



def sv(r1, g1, b1):# настройка сервомотора
    if r1 == 0:
        sv_r.high()
    else:
        sv_r.low()
    if g1 == 0:
        sv_g.high()
    else:
        sv_g.low()
    if b1 == 0:
        sv_b.high()
    else:
        sv_b.low()




# sv(0, 0, 0)
# delay(1000)
# sv(1, 0, 0)
# delay(1000)
# sv(0, 1, 0)
# delay(1000)
# sv(0, 0, 1)
# delay(1000)
# sv(1, 1, 0)
# delay(1000)

while True:# цикл

    # print(kn.value())
    # сообщения RaspBerry
    if uart.any():
        a = chr(uart.readchar())
        if a != "$":
            inn += a
            if len(inn) > 10:
                inn = ""
        else:

            try:
                if len(inn) == 9:
                    speed = int(inn[0:3])-200
                    serv = int(inn[3:6])-200
                    r = int(inn[6:7])
                    g = int(inn[7:8])
                    b = int(inn[8:9])
                    print(speed,serv,r,g,b)
            except ValueError:
                print("err")
            inn = ""
            uart.write(str(kn.value())+"$")





# import pyb
# uart = UART(6, 115200, stop=1)
# message = "123$"
# inn = ''
# serv_deg = ADC("X4")
#
# pic = Pin('Y10', Pin.OUT_PP)
# # p_out.high()
# # p_out.low()
#
# button = Pin('Y9', Pin.IN, Pin.PULL_UP)
# # p_in.value()
#
#
# M1 = Pin('X5', Pin.OUT_PP)
# M2 = Pin('X6', Pin.OUT_PP)
# MS = Pin('X10')
# tim = Timer(4, freq = 10000)
# ch = tim.channel(2, Timer.PWM, pin = MS)
#
#
# S1 = Pin('X7', Pin.OUT_PP)
# S2 = Pin('X8', Pin.OUT_PP)
# SS = Pin('X9')
# tim = Timer(4, freq = 10000)
# chS = tim.channel(1, Timer.PWM, pin = SS)
#
# def Motor(sp):
#     global ch, M1, M2
#     if sp < 0:
#         M1.low()
#         M2.high()
#         sp = -sp
#     else:
#         M2.low()
#         M1.high()
#     ch.pulse_width_percent(sp)
#
# eold = 0
# def Serv(deg):
#     global eold, S1, S2, chS
#     if deg<700:
#         deg = 700
#     if deg > 3000:
#         deg = 3000
#     e = deg - serv_deg.read()
#     u = e * 0.1 + (e - eold)*0.3
#
#     if u < 0:
#         S1.low()
#         S2.high()
#         u = -u
#     else:
#         S2.low()
#         S1.high()
#
#
#     if u > 100:
#         u = 100
#
#     if u < 15:
#         u = 30
#
#     if -50 < e < 50:
#         u = 0
#         S1.low()
#         S2.low()
#
#     chS.pulse_width_percent(u)
#     eold = e
#
#
# flag_start = True
# speed = 0
# rul = 0
#
#
#
# while True:
#     if uart.any():
#         a = chr(uart.readchar())
#         if a != '$':
#             inn += a
#             if len(inn) > 9:
#                 inn = ""
#         else:
#             if flag_start:
#                 if inn == "9999999":
#                     flag_start = False
#                     pic.high()
#                     delay(500)
#                     pic.low()
#             else:
#                 message = 'B=' + str(button.value()) + '$'
#                 try:
#                     if len(inn) == 7 and inn != '9999999':
#                         speed = int(inn[:3])-200
#                         rul = int(inn[3:])-1000
#                         # print(speed, rul)
#                         Motor(speed)
#                         Serv(rul)
#                 except ValueError:
#                     print("err")
#
#             # print(inn)
#             inn = ""
#             uart.write(message)

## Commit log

2023-04-03 Create тест
2023-05-08 Rename test to Ссылка на YouTube
2023-05-08 Update Ссылка на YouTube
